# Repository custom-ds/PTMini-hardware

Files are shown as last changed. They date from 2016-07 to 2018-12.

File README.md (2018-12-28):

# PTMini Flight Tracker
## * Not under current development *
The PTMini was originally intended to be the second generation APRS tracker from the Project: Traveler group, however it has been tabled for the time being.  Instead the ArduinoTrack Flex is under current development.

[ArduinoTrack Flex Project](https://github.com/custom-ds/ArduinoTrack-Flex-Hardware "ArduinoTrack Flex")

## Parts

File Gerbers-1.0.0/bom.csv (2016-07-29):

Part | Value | Device | Package | Description | DIGIKEY | MF | MPN | OC_FARNELL | OC_NEWARK | PROD_ID | VALUE
ANT1 | GPS_ANT_SMDBAR | GPS_ANT_SMDBAR | 1575AT43A40 | 1.575 GHz GPS Antenna Johanson Technology | 712-1003-1-ND
ANT2 | BU-SMA-V | BU-SMA-V | BU-SMA-V | FEMALE SMA CONNECTOR | CONSMA001-ND |  |  | unknown | unknown
C1 | .1uF | C-USC0805 | C0805 | CAPACITOR, American symbol | 311-1361-1-ND
C2 | .1uF | C-USC0805 | C0805 | CAPACITOR, American symbol | 311-1361-1-ND
C3 | .1uF | C-USC0805 | C0805 | CAPACITOR, American symbol | 311-1361-1-ND
C4 | .1uF | C-USC0805 | C0805 | CAPACITOR, American symbol | 311-1361-1-ND
C5 | .1uF | C-USC0805 | C0805 | CAPACITOR, American symbol | 311-1361-1-ND
C6 | .1uF | C-USC0805 | C0805 | CAPACITOR, American symbol | 311-1361-1-ND
C7 | .1uF | C-USC0805 | C0805 | CAPACITOR, American symbol | 311-1361-1-ND
C8 | 20pF | C-USC0805 | C0805 | CAPACITOR, American symbol | 712-1381-1-ND
C9 | 36pF | C-USC0805 | C0805 | CAPACITOR, American symbol | 712-1387-1-ND
C10 | 20pF | C-USC0805 | C0805 | CAPACITOR, American symbol | 712-1381-1-ND
C11 | 47uF | CPOL-US153CLV-0605 | 153CLV-0605 | POLARIZED CAPACITOR, American symbol | PCE3842CT-ND
C12 | .1uF | C-USC0805 | C0805 | CAPACITOR, American symbol | 311-1361-1-ND
C13 | .1uF | C-USC0805 | C0805 | CAPACITOR, American symbol | 311-1361-1-ND
C14 | .1uF | C-USC0805 | C0805 | CAPACITOR, American symbol | 311-1361-1-ND
C15 | .1uF | C-USC0805 | C0805 | CAPACITOR, American symbol | 311-1361-1-ND
C16 | .1uF | C-USC0805 | C0805 | CAPACITOR, American symbol | 311-1361-1-ND
C17 | .1uF | C-USC0805 | C0805 | CAPACITOR, American symbol | 311-1361-1-ND
D1 | LL4148 | LL4148 | SOD-80 | General purpose LL1448 Diode in the SOD-80 (glass tube) form factor. | 568-1749-1-ND
D2 | LL4148 | LL4148 | SOD-80 | General purpose LL1448 Diode in the SOD-80 (glass tube) form factor. | 568-1749-1-ND
D3 | LL4148 | LL4148 | SOD-80 | General purpose LL1448 Diode in the SOD-80 (glass tube) form factor. | 568-1749-1-ND
D4 | LED | LED | DIODE-1206 | Light Emitting Diode (LED) in a 1206 SMT package. | 160-1405-1-ND
D5 | LED | LED | DIODE-1206 | Light Emitting Diode (LED) in a 1206 SMT package. | 160-1169-1-ND
J1 |  | JST_2MM_MALE | JST-2-SMD | Mates to single-cell LiPo batteries. | 455-1749-1-ND |  |  |  |  | CONN-08352
J2 |  | M06RA | MOLEX-1X6-RA | Header 6 | WM4304-ND
J3 |  | M05LOCK | 1X05_LOCK | Header 5 | SAM1112-32-ND
J4 | MINI-USB-UX60A-MB-5ST | MINI-USB-UX60A-MB-5ST | UX60A-MB-5ST | MINI USB Connector | H2961CT-ND |  |  | unknown | unknown
L1 | 68nH | INDUCTOR0805 | 0805 | Inductors | 535-11572-2-ND OR AISC-0805-R068G-TCT-ND
L2 | 68nH | INDUCTOR0805 | 0805 | Inductors | 535-11572-2-ND OR AISC-0805-R068G-TCT-ND
Q1 | MMBT2222A | TRANSISTOR_NPNMMBT2222A | SOT23 | Generic NPN BJT | MMBT2222AFSCT-ND |  |  |  |  | TRANS-08049 | MMBT2222A
R1 | 10k | R-US_R0805 | R0805 | RESISTOR, American symbol | 311-10.0KCRCT-ND
R2 | 10k | R-US_R0805 | R0805 | RESISTOR, American symbol | 311-10.0KCRCT-ND
R3 | 100k | R-US_R0805 | R0805 | RESISTOR, American symbol | 311-100KCRCT-ND
R4 | 47k | R-US_R0805 | R0805 | RESISTOR, American symbol | 311-47.0KCRCT-ND
R5 | 4.7k | R-US_R0805 | R0805 | RESISTOR, American symbol | 311-4.7KARCT-ND
R6 | 4.7k | R-US_R0805 | R0805 | RESISTOR, American symbol | 311-4.7KARCT-ND
R7 | 4.7k | R-US_R0805 | R0805 | RESISTOR, American symbol | 311-4.7KARCT-ND
R8 | 10k | R-US_R0805 | R0805 | RESISTOR, American symbol | 311-10.0KCRCT-ND
SG1 | BUZZERSMD | BUZZERSMD | BUZZER-CMT1603 | Buzzer 12mm | 102-1193-1-ND
U1 | MCP1703DB | MCP1703DB | SOT223 | 250 mA, 16V, Low Quiescent Current LDO Regulator | MCP1703T-3302E/DBCT-ND
U2 | CY8C4248AZI-L485 | CY8C4248AZI-L485 | QFP64_SOT393 |  | 428-3598-ND
U3 | UBLOX-MAX | UBLOX-MAX | UBLOX-MAX | UBlox MAX-series of GPS receiver engines.
U4 | MS5611-01BA03 | MS5611-01BA03 | MS5611-01BA03 | MS5611-01BA03 Barometric Pressure Sensor | 223-1622-1-ND
U5 | EEPROM-I2CSMD | EEPROM-I2CSMD | SO08 | I2C EEPROM chips, 24LC256 (and others) | 24LC64F-I/SN-ND
U6 | DRA818V | DRA818V | SMD_DRA818 | DRA818V is a compact wireless voice transceiver from Dorji.
U7 | PUSBM12VX4-TL-115 | PUSBM12VX4-TL-115 | PUSBM12VX4-TL-115 |  | 568-10918-1-ND

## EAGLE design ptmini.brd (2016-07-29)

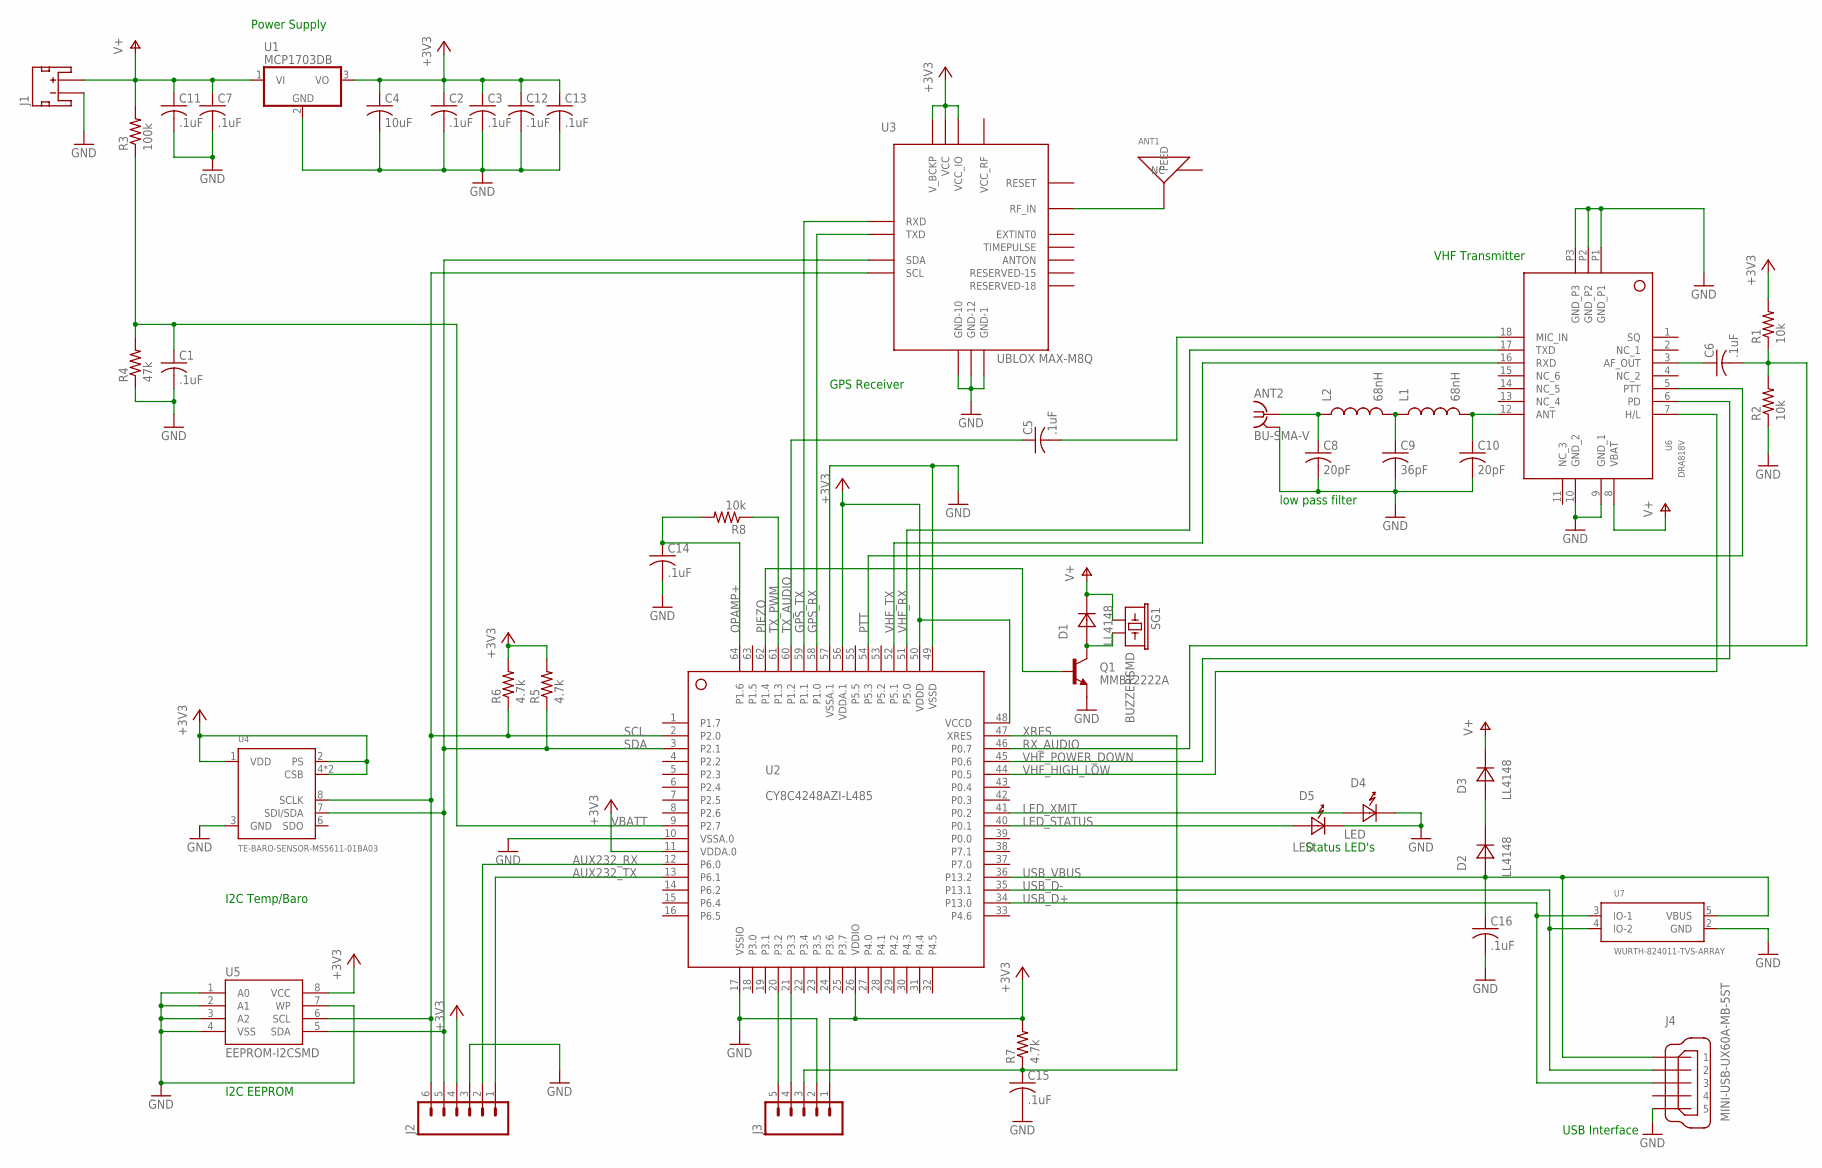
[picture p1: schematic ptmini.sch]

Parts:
ANT1: GPS_ANT_SMDBAR; 1575AT43A40; DIGIKEY 712-1003-1-ND
ANT2: BU-SMA-V; DIGIKEY CONSMA001-ND
C1, C2, C3, C5, C6, C7, C11, C12, C13, C14, C15, C16: .1uF; C0805; DIGIKEY 311-1361-1-ND
C4: 10uF; C0805; DIGIKEY 490-3886-1-ND
C8, C10: 20pF; C0805; DIGIKEY 712-1381-1-ND
C9: 36pF; C0805; DIGIKEY 712-1387-1-ND
D1, D2, D3: LL4148; SOD-80; DIGIKEY 568-1749-1-ND
D4: LED; DIODE-1206; DIGIKEY 160-1405-1-ND
D5: LED; DIODE-1206; DIGIKEY 160-1169-1-ND
J1: JST_2MM_MALE; JST-2-SMD; DIGIKEY 455-1749-1-ND
J2: M06RA; MOLEX-1X6-RA; DIGIKEY WM4304-ND
J3: M05LOCK; 1X05_LOCK; DIGIKEY SAM1112-32-ND
J4: MINI-USB-UX60A-MB-5ST; UX60A-MB-5ST; DIGIKEY H2961CT-ND
L1, L2: 68nH; 0805; DIGIKEY AISC-0805-R068G-TCT-ND
Q1: MMBT2222A; SOT23; DIGIKEY MMBT2222AFSCT-ND
R1, R2, R8: 10k; R0805; DIGIKEY 311-10.0KCRCT-ND
R3: 100k; R0805; DIGIKEY 311-100KCRCT-ND
R4: 47k; R0805; DIGIKEY 311-47.0KCRCT-ND
R5, R6, R7: 4.7k; R0805; DIGIKEY 311-4.7KARCT-ND
SG1: BUZZERSMD; BUZZER-CMT1603; DIGIKEY 102-1193-1-ND
U1: MCP1703DB; SOT223; DIGIKEY MCP1703T-3302E/DBCT-ND
U2: CY8C4248AZI-L485; TQFP64-10X10; DIGIKEY 428-3598-ND
U3: UBLOX MAX-M8Q; UBLOX-MAX
U4: TE-BARO-SENSOR-MS5611-01BA03; TE-BARO-SENSOR-MS5611-01BA3; DIGIKEY 223-1622-1-ND
U5: EEPROM-I2CSMD; SO08; DIGIKEY 24LC64F-I/SN-ND
U6: DRA818V; SMD_DRA818
U7: WURTH-824011-TVS-ARRAY; SOT23-5; DIGIKEY 732-4465-1-ND

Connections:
+3V3: C2.1, C3.1, C4.1, C12.1, C13.1, J2.4, J3.1, R1.2, R5.2, R6.2, R7.2, U1.3 (VO), U2.11 (VDDA.0), U2.26 (VDDIO), U2.48 (VCCD), U2.50 (VDDD), U2.56 (VDDA.1), U3.6_V_BCKP (V_BCKP), U3.7_VCC_IO (VCC_IO), U3.8_VCC (VCC), U4.1 (VDD), U4.2 (PS), U4.4 (CSB), U4.5 (CSB), U5.8 (VCC)
AUX232_RX: J2.2, U2.12 (P6.0)
AUX232_TX: J2.1, U2.13 (P6.1)
GND: ANT2.2, ANT2.3 (2), ANT2.4 (2), ANT2.5 (2), C1.2, C2.2, C3.2, C4.2, C7.2, C8.2, C9.2, C10.2, C11.2, C12.2, C13.2, C14.2, C15.2, C16.2, D4.CATHODE, D5.CATHODE, J1.1 (-), J2.3, J3.2, J4.5, Q1.2 (E), R2.1, R4.1, U1.2 (GND), U2.10 (VSSA.0), U2.17 (VSSIO), U2.49 (VSSD), U2.57 (VSSA.1), U3.1_GND (GND-1), U3.10_GND (GND-10), U3.12_GND (GND-12), U4.3 (GND), U5.1 (A0), U5.2 (A1), U5.3 (A2), U5.4 (VSS), U5.7 (WP), U6.9 (GND_1), U6.10 (GND_2), U6.P1 (GND_P1), U6.P2 (GND_P2), U6.P3 (GND_P3), U7.2 (GND)
GPS_RX: U2.58 (P1.0), U3.2_TXD1 (TXD)
GPS_TX: U2.59 (P1.1), U3.3_RXD1 (RXD)
LED_STATUS: D5.ANODE, U2.40 (P0.1)
LED_XMIT: D4.ANODE, U2.41 (P0.2)
unnamed: D1.ANODE, Q1.3 (C), SG1.P$2 (2)
unnamed: C5.2, U6.18 (MIC_IN)
unnamed: ANT1.FEED, U3.11_RF_IN (RF_IN)
unnamed: D2.CATHODE, D3.ANODE
unnamed: C6.1, U6.3 (AF_OUT)
unnamed: ANT2.1, C8.1, L2.1
unnamed: C9.1, L1.1, L2.2
unnamed: C10.1, L1.2, U6.12 (ANT)
unnamed: J3.5, U2.20 (P3.2)
unnamed: J3.4, U2.21 (P3.3)
OPAMP+: C14.1, R8.2, U2.64 (P1.6)
PIEZO: Q1.1 (B), U2.62 (P1.4)
PTT: U2.54 (P5.3), U6.5 (PTT)
RESET: U3.9_V_RESET (RESET)
RX_AUDIO: C6.2, R1.1, R2.2, U2.46 (P0.7)
SCL: J2.6, R6.1, U2.2 (P2.0), U3.17_SCL2 (SCL), U4.8 (SCLK), U5.6 (SCL)
SDA: J2.5, R5.1, U2.3 (P2.1), U3.16_SDA2 (SDA), U4.7 (SDI/SDA), U5.5 (SDA)
TX_AUDIO: C5.1, U2.60 (P1.2)
TX_PWM: R8.1, U2.61 (P1.3)
USB_D+: J4.3, U2.34 (P13.0), U7.3 (IO-1)
USB_D-: J4.2, U2.35 (P13.1), U7.4 (IO-2)
USB_VBUS: C16.1, D2.ANODE, J4.1, U2.36 (P13.2), U7.5 (VBUS)
V+: C7.1, C11.1, D1.CATHODE, D3.CATHODE, J1.2 (+), R3.2, SG1.P$1 (1), U1.1 (VI), U6.8 (VBAT)
VBATT: C1.1, R3.1, R4.2, U2.9 (P2.7)
VHF_HIGH_LOW: U2.44 (P0.5), U6.7 (H/L)
VHF_POWER_DOWN: U2.45 (P0.6), U6.6 (PD)
VHF_RX: U2.51 (P5.0), U6.17 (TXD)
VHF_TX: U2.52 (P5.1), U6.16 (RXD)
XRES: C15.1, J3.3, R7.1, U2.47 (XRES)

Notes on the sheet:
low pass filter
Status LED's
USB Interface
VHF Transmitter
GPS Receiver
Power Supply
I2C Temp/Baro
I2C EEPROM

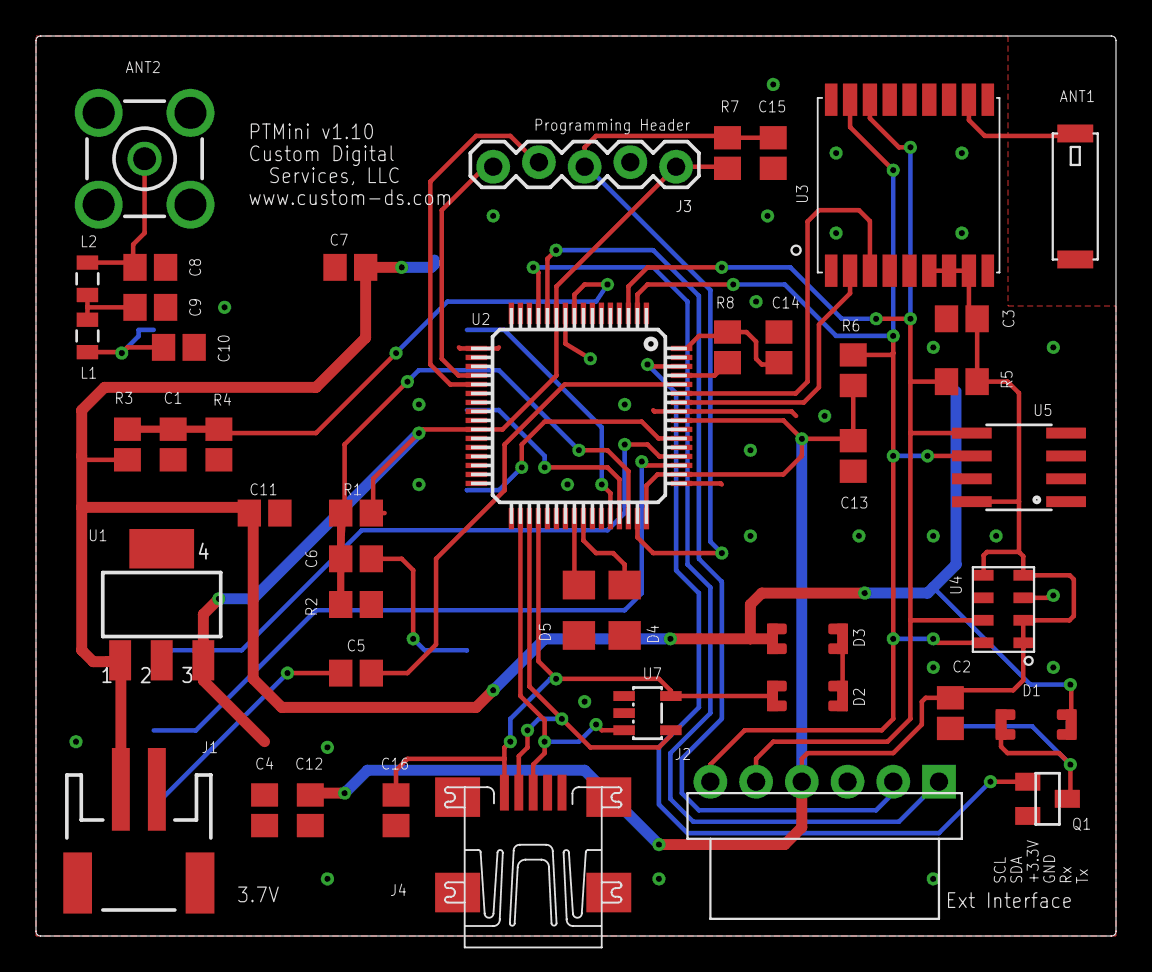
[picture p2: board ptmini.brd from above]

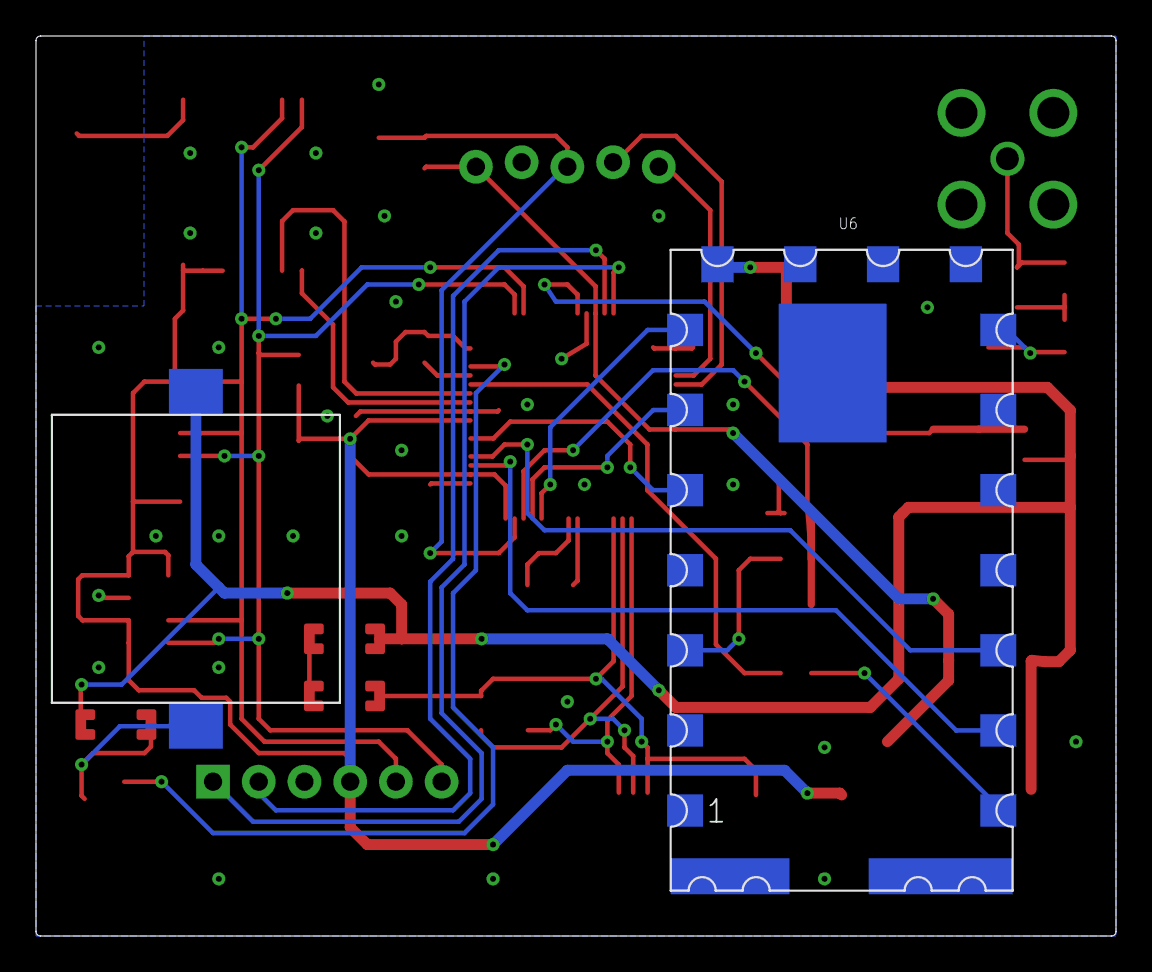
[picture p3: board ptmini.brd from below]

Board: 2 copper layers, 60.0 x 50.0 mm, 46 parts (2 on the bottom side), 36 nets.

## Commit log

2016-07-15 Board version 1.00
    First run at the PTMini PCB. Placed the VHF model on the back of the
    board. Most of the Digikey part numbers are keyed in, but a few are
    still outstanding.
    [ptmini.gbr]
2016-07-17 Board version 1.01.
    Minor changes to a few of the component libraries. Swapped out the
    diodes with a smaller LL4148 diode. Defined all component values and
    Digikey part numbers. Set values for low pass filter. Renumbered board
    to 1.01 to reflect the slight layout changes. All components remain
    unchanged otherwise.
    [ptmini.brd, ptmini.sch]
2016-07-29 Board version 1.1.0
    Fixed incorrect chip footprint for PSoC chip, and also a bad power
    connection to the chip. Relocated the piezo to the back side of the PCB
    and consolidated down to 5cm x 6cm.
    [bom.csv, ptmini.brd, ptmini.sch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]

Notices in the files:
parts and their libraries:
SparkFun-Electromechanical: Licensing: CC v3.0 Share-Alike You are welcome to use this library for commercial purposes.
